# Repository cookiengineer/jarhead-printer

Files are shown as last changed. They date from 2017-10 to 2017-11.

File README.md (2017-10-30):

# Jarhead Printer

The Jarhead Printer is a 3D printer / CNC that is built to endure
heavy environments and still allowing maximum print precision and
quality.

It is originally derived from several other designs, such as the
Prusa i3, Anet AM8, OpenBuilds' Printbot and other printers. You
can see it as the evil cross-breed that tries to use advantages
of all other designs while trying to keep its design as simple
(and interchangeable) as possible.

However, the main focus of this printer is to being "built to endure"
so its design and its parts follow the KISS principle and still try
to allow flexible modifications and scaling of X/Y/Z print volume
dimensions.

## Features Overview

- 3D Printer for ABS, PLA, PETG
- CNC for Aluminium, Wood and Plastics
- Very sturdy, bubble-leveled frame
- X-Cart designed for replaceable tools
- Y-Cart designed for replaceable beds
- Interchangeable, simple part design
- Compatible with E3D V6 Bowden Extruder
- Cork- and Fiberglass-insulated heatbed

# Preview Pictures

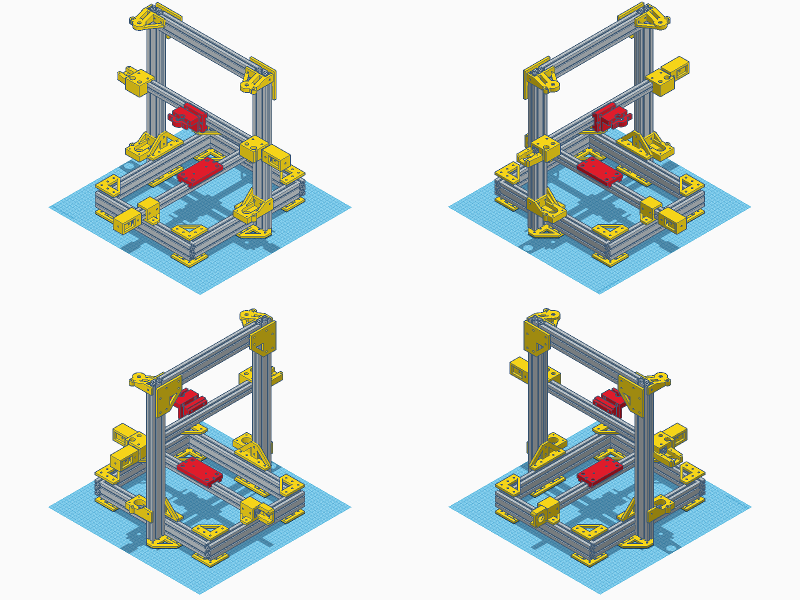
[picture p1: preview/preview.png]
preview


## Print Settings

Print Settings:

```
material:             PLA (or ABS)
layer height:         0.2mm
wall thickness:       0.8mm
top/bottom thickness: 0.8mm
infill density:       80%
infill pattern:       tetrahedral
```

**ABS**:

If you want to use the 3D printer as an ABS and PETG printer,
it is recommended to print the `tools` parts with ABS so that
those can withstand higher temperatures.

# Bill of Materials / Print Checklist

As the Jarhead Printer is a configurable printer that is flexible
in its design, dimensions, tools and parts - there is a web app
available that helps you choose what you want:

[Jarhead Configurator](https://rawgit.com/cookiengineer/jarhead-printer/master/configurator/index.html)

If you want to make the defaulted printer, you can still follow
the oldschool [BOM.md](./BOM.md). Note that the printer is RAMPS
compatible, so a standard RAMPS Kit and Hotbed are implied when
building for an E3D V6 Hotend.

# Work in Progress

- Extruder Motor Design
- Mainboard Mount Design
- Power Supply Mount Design
- Firmware (probably a Marlin fork)

# FAQ

- How's the name "Jarhead" related to this?
  1. It looks like a jar.
  2. It tries to achieve military precision.
  3. It has replaceable heads.
  4. ...
  5. I guess you get it now.

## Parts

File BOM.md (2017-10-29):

# Bill of Materials

## Printable Parts

**Frame**:

- [1x Z Endstop](./design/frame/1xZ_Endstop.stl)
- [1x Z Motor Mount Left](./design/frame/1xZ_Motor_Mount_Left.stl)
- [1x Z Motor Mount Right](./design/frame/1xZ_Motor_Mount_Right.stl)
- [1x Z Rod Holder Left](./design/frame/1xZ_Rod_Holder_Left.stl)
- [1x Z Rod Holder Right](./design/frame/1xZ_Rod_Holder_Right.stl)
- [2x Bottom Tee Plate](./design/frame/2xBottom_Tee_Plate.stl)
- [2x Side Tee Corner](./design/frame/2xSide_Tee_Corner.stl)
- [2x Top Corner Plate](./design/frame/2xTop_Corner_Plate.stl)
- [8x Bottom Corner Plate](./design/frame/8xBottom_Corner_Plate.stl)

**X-Carriage**:

The default X-Cart matches the specifications for Openbuilds Delrin Mini V Wheels.
The X-Left and X-Right parts must be mirrored (along the X-axis) to be used on the other side.

- [1x X-Cart](./design/x-carriage/1xX-Cart.stl) or alternatively [1x X-Cart for 605ZZ Wheels](./design/x-carriage/1xX-Cart_for_605ZZ_Wheels.stl)
- [1x X-Left with Motor Mount](./design/x-carriage/1xX-Left_with_Motor_Mount.stl)
- [1x X-Right with Belt Puller](./design/x-carriage/1xX-Right_with_Belt_Puller.stl)

**Y-Carriage**:

The default Y-Cart matches the specifications for Openbuilds Delrin Mini V Wheels.
The Y-Top and Y-Bottom parts can be used on both sides.

- [1x Y-Cart](./design/y-carriage/1xY-Cart.stl) or alternatively [1x Y-Cart for 605ZZ Wheels](./design/y-carriage/1xY-Cart_for_605ZZ_Wheels.stl)
- [1x Y-Front with Belt Puller](./design/y-carriage/1xY-Front_with_Belt_Puller.stl)
- [1x Y-Rear with Motor Mount](./design/y-carriage/1xY-Rear_with_Motor_Mount.stl)

**Tools**:

The default E3D Tool Plate has no belt grip. If the part is printed on a 3D printer with
very good precision, it is recommended to print the variant with a Belt Grip.

- [1x E3D Tool Cap](./design/tools/1xE3D_Tool_Cap.stl)
- [1x E3D Tool Plate](./design/tools/1xE3D_Tool_Plate.stl) or alternatively [1x E3D Tool Plate with Belt Grip](./design/tools/1xE3D_Tool_Plate_with_Belt_Grip.stl)

**Other Parts**:

The default Belt Tensioner matches the specifications for Openbuilds Pulley Idler Wheel.

- [2x Belt Tensioner](./design/tensioner/2xBelt_Tensioner.stl)
- [2x Belt Tensioner Knob](./design/tensioner/2xBelt_Tensioner_Knob.stl)
- [2x GT20 Idler](./design/parts/2xGT20_Idler.stl)
- [2x GT20 Pulley](./design/parts/2xGT20_Pulley.stl)
- [8x 605ZZ Wheel](./design/parts/8x605ZZ_Wheel.stl)
- [M5 T-Slot Nut](./design/parts/M5_T-Slot_Nut.stl)

## Bill of Materials

**Frame Parts**

The printer frame is built with `2040` extrusions while the
X-Axis (that moves the extruder) and Y-Axis (that moves the heatbed)
use `2020` extrusions.

Every frame dimension is freely scaleable, as all printable parts
are prepared for that use case. Please use the [calculator](https://rawgit.com/cookiengineer/jarhead-printer/master/calculator/index.html)
that is included in this repository.

| Amount | Description | Length | Usage |
|---|---|---|---|
| 1x | 2020 Aluminium Profile B-Type Nut 6 | 425mm  | X-Axis |
| 1x | 2020 Aluminium Profile B-Type Nut 6 | 380mm  | Y-Axis |
| 2x | 2040 Aluminium Profile B-Type Nut 6 | 440mm  | Z-Frame (Left and Right) |
| 2x | 2040 Aluminium Profile B-Type Nut 6 | 340mm  | Y-Frame (Left and Right) |
| 3x | 2040 Aluminium Profile B-Type Nut 6 | 310mm  | X-Frame (Front, Rear and Middle ) |
| 2x | 8mm Rod | 360mm  | Z-Axis |
| 2x | 8mm Threaded Rod | 355mm  | Z-Axis |

**Electronics**

| Amount | Description |
|---|---|
| 1x | E3D V6 Hotend |
| 1x | Hotbed MK2B 200mm x 200mm |
| 1x | RAMPS Kit with 5 motor drivers and LCD |
| 5x | NEMA17 Stepper Motor |

If you want to use a different Hotbed size, adjust the X and Y dimension
for the frame parts accordingly.

**Mechanical Parts**

| Amount | Description | Usage |
|---|---|---|
| 2x | ABEC-5 608ZZ Bearing | Threaded Rods to Z-Rod Holder |
| 16x | ABEC-5 605ZZ Bearing | X-Cart Wheels, Y-Cart Wheels |
| 2x | LM8UU Bearing | X-Left and X-Right to Z-Rods |
| 16x | M3x20mm Bolt | Stepper Motors |
| 8x | M5 Nut | Tool Plate, X-Cart, Y-Cart, Tensioners |
| 6x | M5 Washer | X-Cart Wheels, Y-Cart Wheels, Tensioners |
| 10x | M5 self-locking Nut | X-Cart Wheels, Y-Cart Wheels |
| 92x | M5 T-Slot Nut | Frame |
| 92x | M5x10mm Bolt | Frame |
| 4x | M5x16mm Bolt | X-Cart to Tool Plate, Y-Cart to Heatbed Plate |
| 14x | M5x30mm Bolt | X-Cart Wheels, Y-Cart Wheels, Tool Plate |
| 4x | M6x20mm Bolt | Z-Frame to Bottom Tee Plate |
| 2x | M8 Nut | Threaded Rods to X-Left and X-Right |
| 8x | Openbuilds Delrin Mini-V Wheel | X-Cart Wheels, Y-Cart Wheels |
| 2x | 5x8mm Aluminium Z-Coupler | Stepper Motors to Z-Rods |

The default X-Cart and Y-Cart design is compatible with the Openbuilds Delrin
Mini V Wheels and if those are used the 605ZZ bearings are not required.

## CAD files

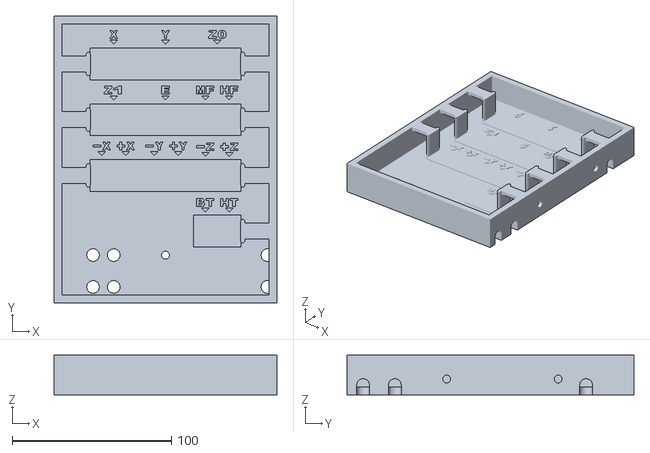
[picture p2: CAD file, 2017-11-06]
design/electronics/1xSwitchboard.stl
140.0 x 180.0 x 25.0

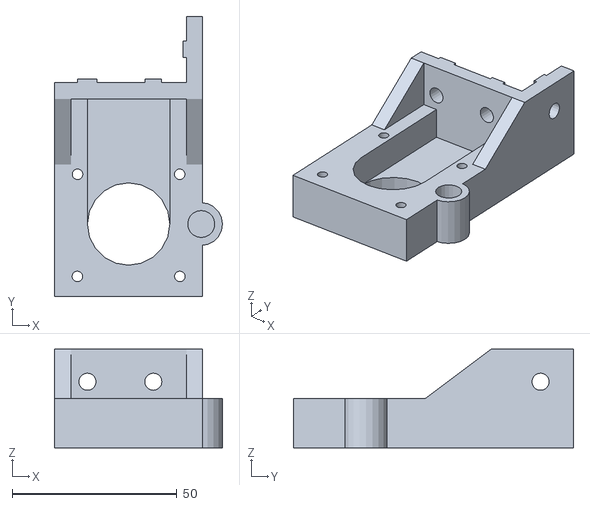
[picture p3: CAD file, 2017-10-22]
design/frame/1xZ_Motor_Mount_Right.stl
51.0 x 85.0 x 30.0

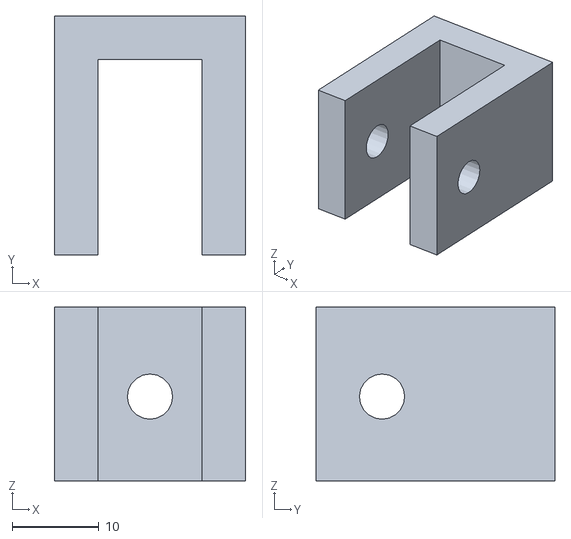
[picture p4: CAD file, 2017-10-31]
design/parts/2xBelt_Tensioner.stl
22.0 x 27.5 x 20.0

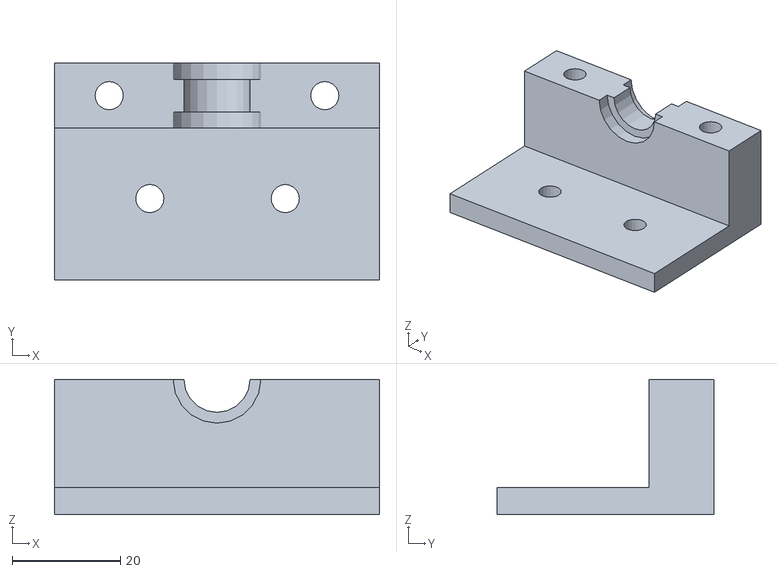
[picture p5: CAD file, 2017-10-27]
design/tools/1xE3D_Tool_Plate.stl
60.0 x 40.0 x 25.0

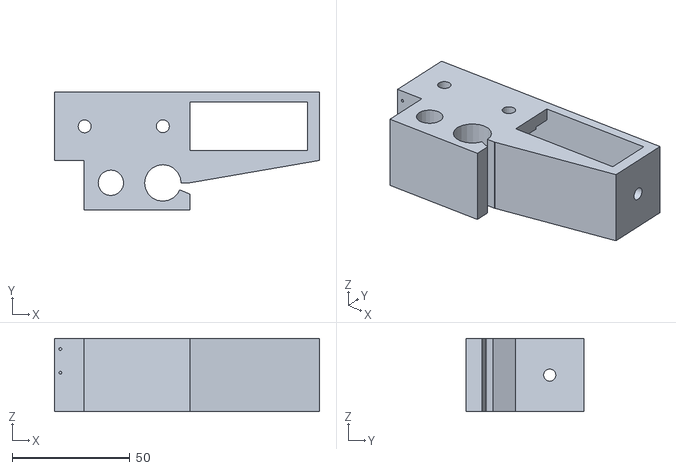
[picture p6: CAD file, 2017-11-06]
design/x-carriage/1xX-Right_with_Belt_Puller.stl
112.5 x 50.0 x 31.0

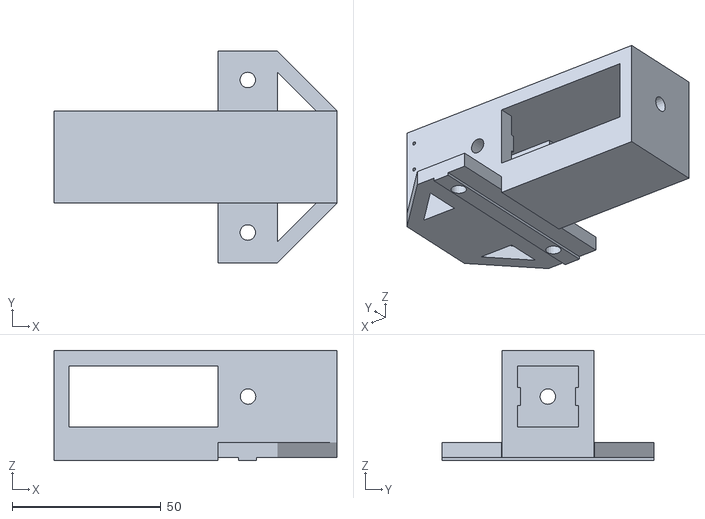
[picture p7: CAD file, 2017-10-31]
design/y-carriage/1xY-Front_with_Belt_Puller.stl
95.0 x 71.0 x 37.0

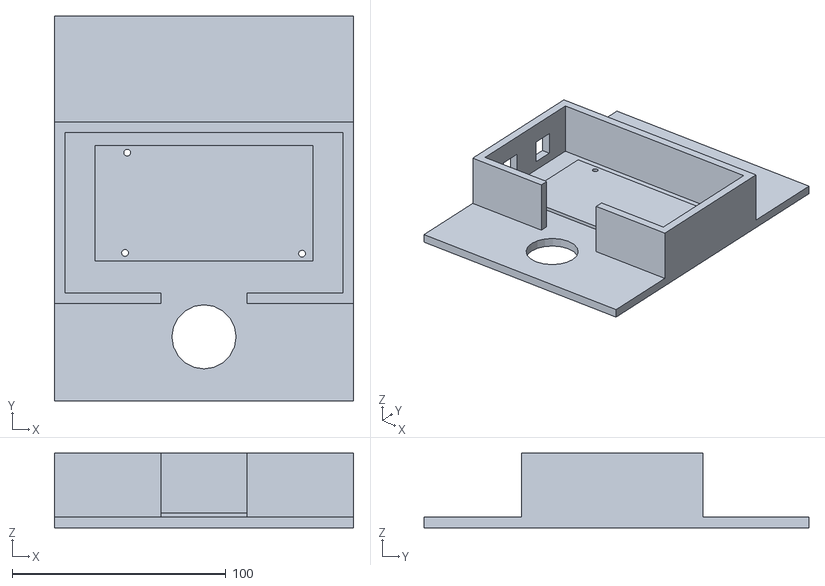
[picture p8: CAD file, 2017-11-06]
design/electronics/1xRAMPS.stl
140.0 x 180.0 x 35.0

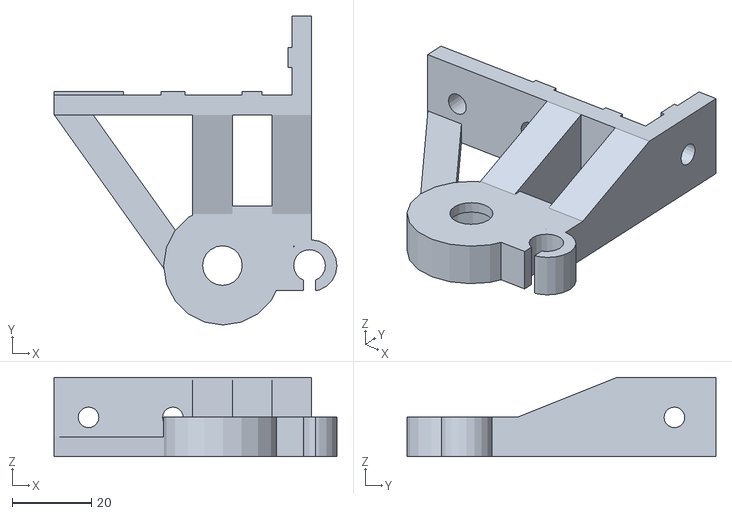
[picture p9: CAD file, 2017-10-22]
design/frame/1xZ_Rod_Holder_Right.stl
71.4 x 78.0 x 20.0

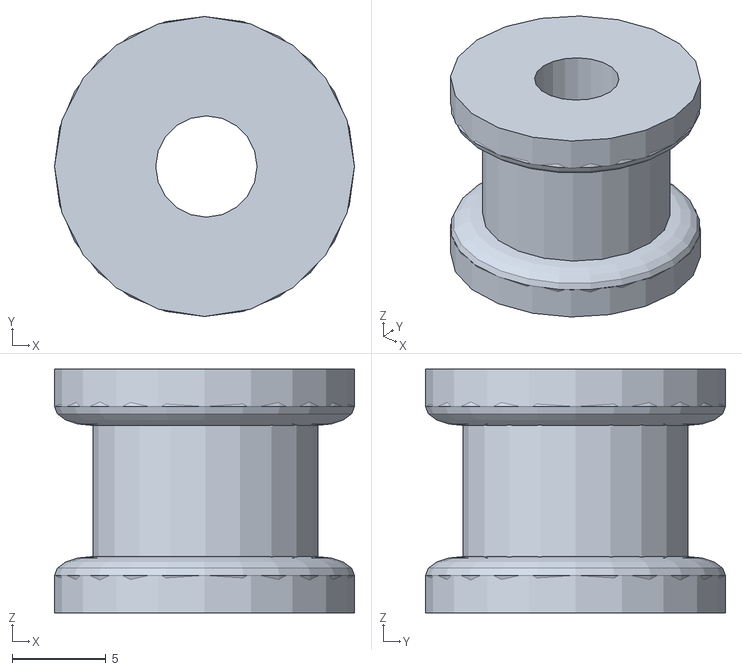
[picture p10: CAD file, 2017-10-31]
design/parts/2xFlat_Idler.stl
16.0 x 16.0 x 13.0

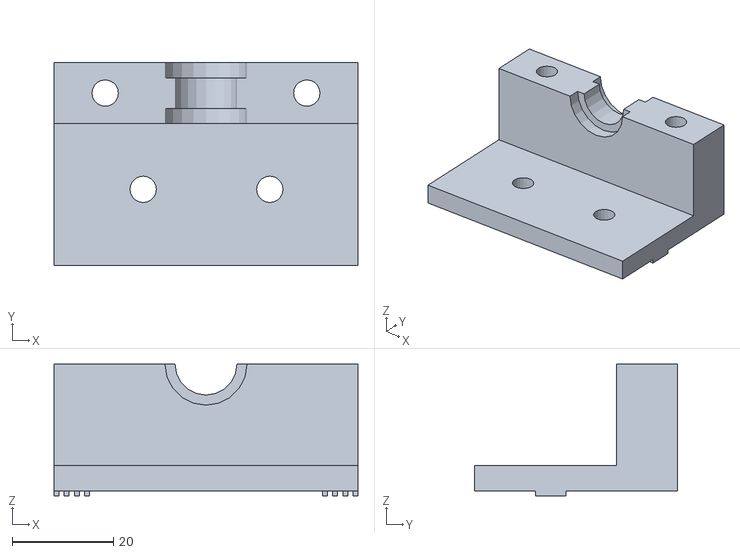
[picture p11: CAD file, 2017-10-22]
design/tools/1xE3D_Tool_Plate_with_Belt_Grip.stl
60.0 x 40.0 x 26.0

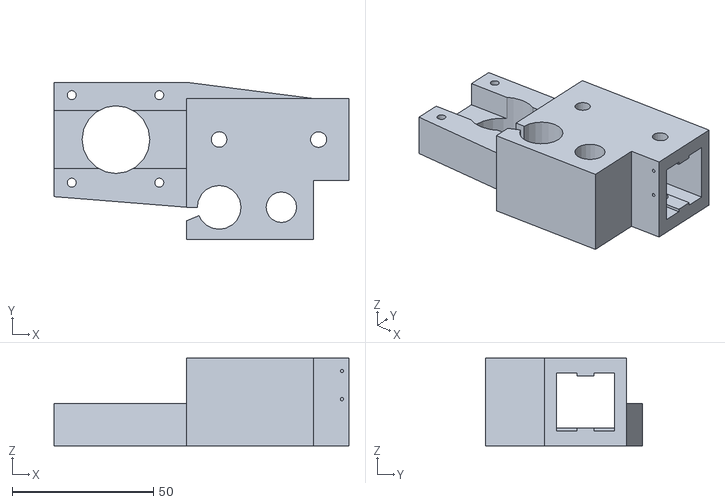
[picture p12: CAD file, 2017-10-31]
design/x-carriage/1xX-Left_with_Motor_Mount.stl
104.5 x 55.8 x 31.0

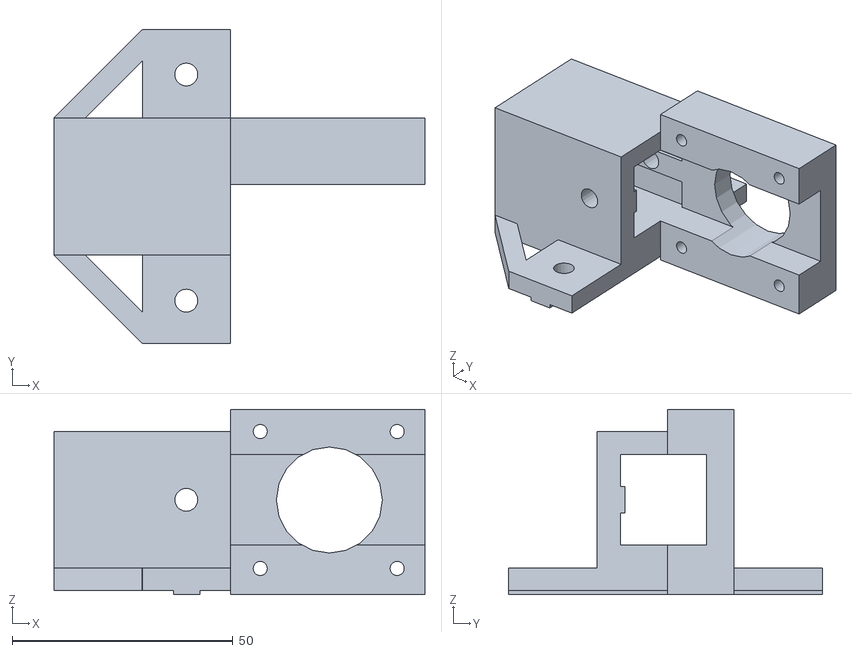
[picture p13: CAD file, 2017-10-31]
design/y-carriage/1xY-Rear_with_Motor_Mount.stl
84.0 x 71.0 x 42.0

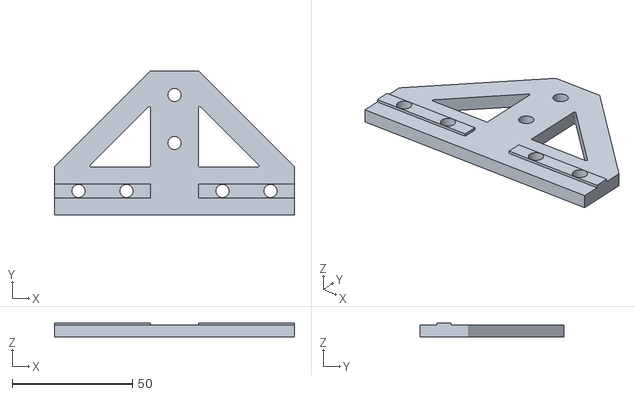
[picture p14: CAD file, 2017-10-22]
design/frame/2xBottom_Tee_Plate.stl
100.0 x 60.0 x 6.00

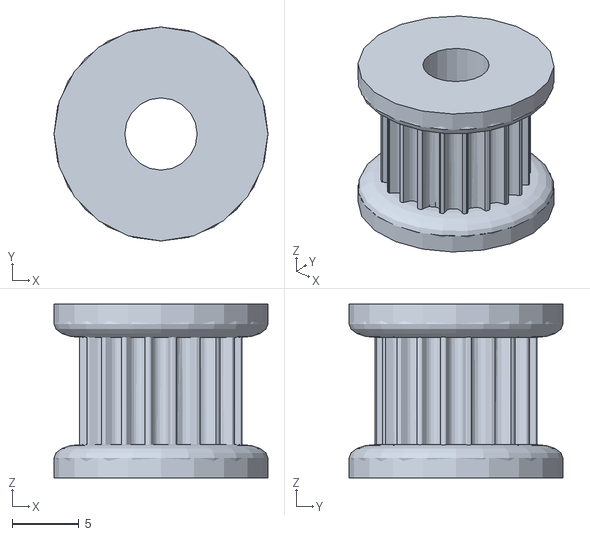
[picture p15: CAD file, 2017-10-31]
design/parts/2xGT20_Idler.stl
16.0 x 16.0 x 13.0

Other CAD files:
design/tools/1xE3D_Tool_Cap.stl
design/x-carriage/1xX-Cart_for_605ZZ_Wheels.stl
design/y-carriage/1xY-Cart_for_605ZZ_Wheels.stl
design/frame/1xZ_Motor_Mount_Left.stl
design/frame/1xZ_Endstop.stl
design/frame/1xZ_Rod_Holder_Left.stl
design/frame/2xSide_Tee_Corner.stl
design/frame/2xTop_Corner_Plate.stl
design/frame/8xBottom_Corner_Plate.stl
design/parts/2xBelt_Tensioner_Knob.stl
design/parts/2xGT20_Pulley.stl
design/parts/8x605ZZ_Wheel.stl
design/parts/M5_T_Nut.stl
design/x-carriage/1xX-Cart.stl
design/y-carriage/1xY-Cart.stl

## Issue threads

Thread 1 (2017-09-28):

Carriage (Re-) Design

cookiengineer, 2017-09-28:
The current prototype of the design sketches for the X-carriage probably aren't working because they use more space than the previous parts. This is a list of parts that have to be redesigned and what has to be done once the final parts are shipped and able to be measured.

- [x] Integrate X-Motor Holder into X-Drive left
- [x] Check dimensions (M8 rod / M10 nut for threaded rod) of X-Drive left and right
- [x] Move Z-Motor Holders both min. 5mm away from Z-frame alu profile
- [x] Move Z-Rod Holders both min. 5mm away from Z-frame alu profile and make them a 3x2 part, so that M5 screws will hold them in place on the middle part of the Z-frame.

After that, the belt tensioners have to be redesigned. It makes sense to probably use a similar design to the Tronxy X3, but will more material in XZ and XY force direction to support the parts.

- [x] Redesign Y-Belt Tensioner to match the stiff M5 design of the other parts
- [x] Redesign X-Belt Tensioner to match the stiff M5 design of the other parts

Closed 2017-10-04.

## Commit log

2017-10-22 :snowflake: Initial commit
    [1xE3D_Tool_Cap.stl, 1xE3D_Tool_Plate.stl, 1xX_Cart.stl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]
2017-10-27 :rocket: Y-Cart for 605ZZ Wheels, E3D Tool Plate for low-precision printers
    [1xE3D_Tool_Plate_without_Belt_Holder.stl, 1xY_Cart_for_605ZZ_V_Wheels.stl, 605ZZ_V_Wheel.stl]
2017-10-29 :snowflake: Better parts, better structure, calculator
    [1xE3D_Tool_Plate.stl, 1xE3D_Tool_Plate_with_Belt_Grip.stl, 1xE3D_Tool_Plate_without_Belt_Holder.stl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]
2017-10-29 :rocket: Jarhead Configurator
    [1xY-Cart_for_605ZZ_Wheels.stl, 1xY-Front_with_Belt_Puller.stl, 1xY-Rear_with_Motor_Mount.stl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]
2017-10-30 :rocket: Endstop Integration
    [1xX-Left_with_Motor_Mount.stl, 1xX-Right_with_Belt_Puller.stl, 1xY-Front_with_Belt_Puller.stl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]
2017-10-30 :bug: Fix for Carts and Endstops
    [1xX-Cart_for_605ZZ_Wheels.stl, 1xY-Cart_for_605ZZ_Wheels.stl]
2017-10-31 :rocket: Alu Parts, PLA Parts and Tensioners
    [2xBelt_Tensioner.stl, 2xFlat_Idler.stl, 2xGT20_Idler.stl]
2017-10-31 :snowflake: Better Belt Tensioners and Pullers, better Configurator
    [1xX-Left_with_Motor_Mount.stl, 1xX-Right_with_Belt_Puller.stl, 1xY-Front_with_Belt_Puller.stl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]
2017-11-06 :snowflake: Electronics
    [1xRAMPS.stl, 1xSwitchboard.stl, 1xX-Right_with_Belt_Puller.stl]
